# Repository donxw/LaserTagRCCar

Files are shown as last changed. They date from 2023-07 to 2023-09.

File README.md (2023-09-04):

# LaserTagRCCar
ESP Now based RC Car and controller with Laser and Photodetector to play Tag

CoverShot

Remote control car and joystick wireless controller with a display showing life left.  Each car has an LED (replaced the laser for child safety) and a photoresistor to sense a "hit".  The RC Car and controller communicate wirelessly using the ESP-NOW communication link.
## Bill of Materials
### Car
* 3D printed parts
* NodeMCU ESP8266 30pin Dev board
* ESP12E Motor Shield HW-588A.  Do not purchase an ESP8266 Motor Shield if it is not marked as HW-588A.
* 2x 6V, 500 RPM N20 Gearmotor.  Faster motors will work as well, but are more difficult to control (especially at low speeds)
* 9V USB rechargable LiPo battery
* 1x Neopixel LED (5mm, 3.3V)
* 1x Clear LED
* 1x Photoresistor (5506)
* 1x 20K Resistor
* 2x 73mm x 3mm O-ring (McMaster-Carr)
* Screws:
  * 1x M2x5
  * 5x M2x6
  * 2x M2x8
  * 3x M2.6x6
  * 2x M3x6
  * 2x M3x16
### Remote Control
* 3D printed parts
* TTGO T-Display ESP32 Board
* Joystick (https://www.mouser.com/ProductDetail/611-THB001P)
* 380 mAH Lipo battery
* Slide switch (https://www.aliexpress.us/item/2251832535125782.html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)

## Assembly
### Assemble Chassis
AssembleChassis_1
AssembleChassis_2
AssembleChassis_3

### Assemble Body
AssembleBody

### Car Wiring
Schematic
NeopixelLEDPinOut
CarWiring

### Remote Control Wiring
RemoteControlSchematic
16_WireRCParts

Slide Switch 
SlideSwitch-AliExpress

### Car Code
Before flasing the code to the car, the MAC of the ESP32 dev board in the Remote Control unit needs to be obtained and put into the ESP8266 arduino code for the car.  This can be done by uploading the code to the remote control unit ESP32 and watching the Serial Port for the MAC.  Copy this, and put the ESP32 address into the code for the ESP8266 of the car.  Now flash the car code and watch the Serial Port for the ESP8266 MAC.  Copy this and put it into the remote control unit ESP32 code, then re-flash the ESP32.

The car code is titled: "NodeMCUMotorShield_RCCar_Receiver_Laser_BiDir_Photosensor.ino".  Use board NodeMCU 1.0.

The remote control code is titled:  "Joystick_send_TTGO_BiDirectional.ino"  Use board ESP32 Dev Module.  This code uses the TFT_eSPI library for the TFT so update the User_Setup_Select.h file to uncomment this setup line only: #include <User_Setups/Setup25_TTGO_T_Display.h>.

Test to be sure the remote control and car communicate to each other before final assembly.

### Complete Car Assembly
After flashing the code to the car, place the body onto the chassis taking care to tuck wiring in without getting under the on-off push button.  Flip the car over to insert fasteners and the 9V usb rechargable battery.
AttachBodyandBattery

To assemble the front wheels, locate the smaller set of wheels and 2x M2 x 16 screws.  Take the screw and push them through the wheel holes to clean out the thin layer of support material left from printing.  Pushing the screw in from the reverse direction works fine.  Or use a 3mm drill bit and clean out the hole with a hand drill.  Once cleaned put a small drop of oil on the screw and push it in the correct direction - see image 3.
PrepIdleWheels

Attach the front wheels, taking care to be sure the wheels are aligned correctly.  Attache the rear wheels to the motor by aligning the flat side of the motor shaft to the flat part of the hole in the wheel.  Stretch the 75mm x 3mm o-ring over the wheels into the v-groove.  Snap on the hood scoop.
Wheels_Oring_Scoop

#### Assemble Remote Control
AssembleRemote

### Final car and remote control appearance 
Complete

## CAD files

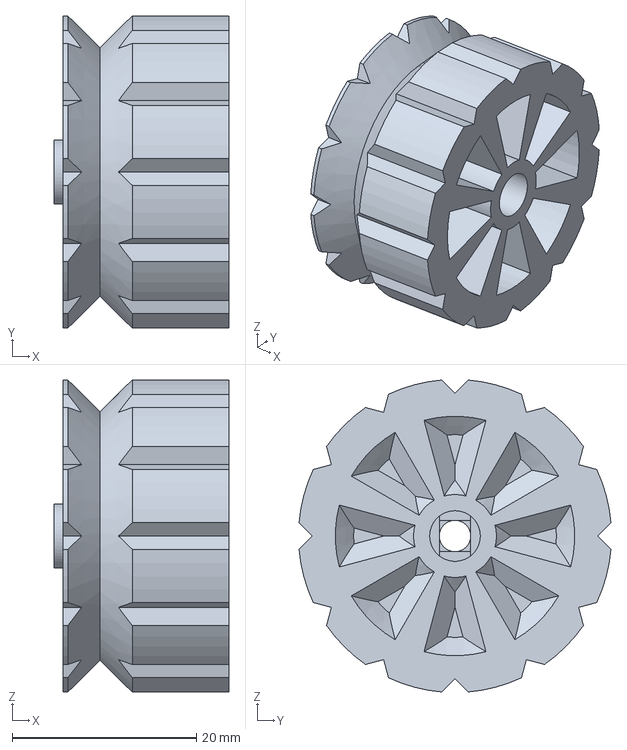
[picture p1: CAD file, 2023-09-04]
StepFiles/IdleWheel.step
19.0 x 33.9 x 33.9 mm

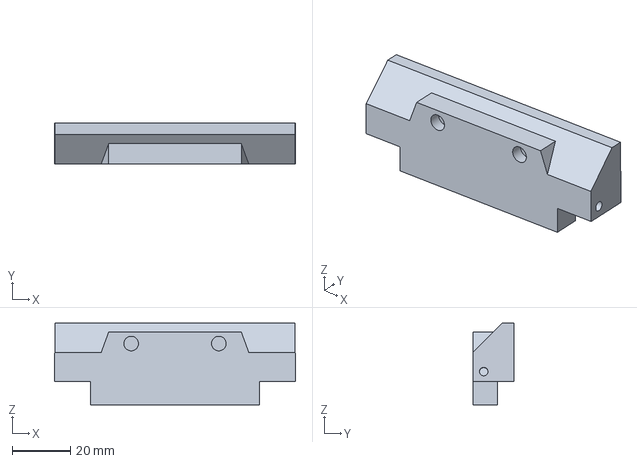
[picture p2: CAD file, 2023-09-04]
StepFiles/FrontAxle.step
82.5 x 14.0 x 28.0 mm

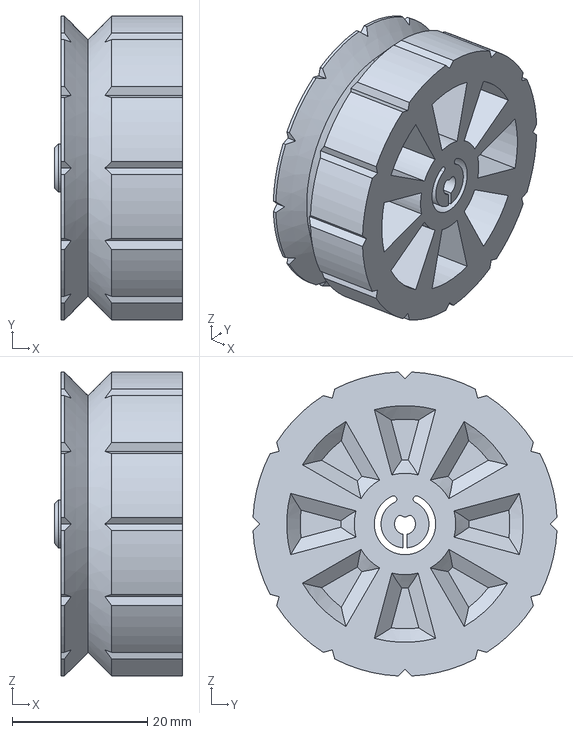
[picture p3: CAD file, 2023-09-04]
StepFiles/DriveWheel.step
19.0 x 45.0 x 45.0 mm

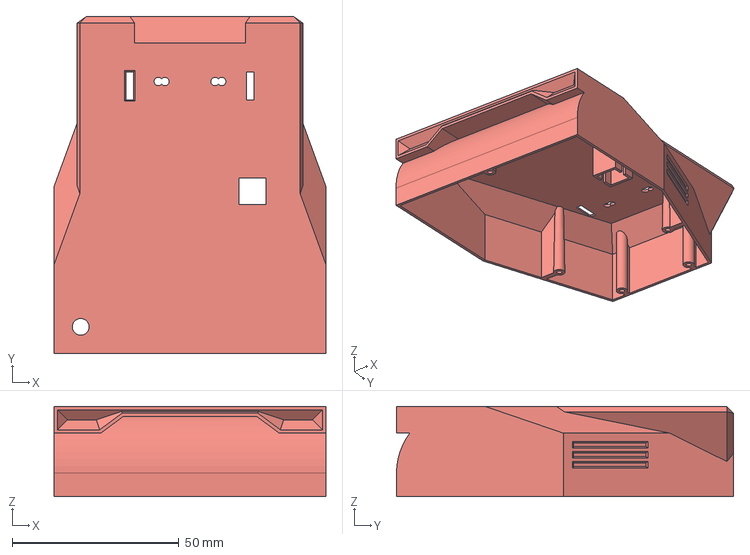
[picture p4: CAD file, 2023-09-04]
StepFiles/Body.step
81.5 x 101.0 x 27.0 mm

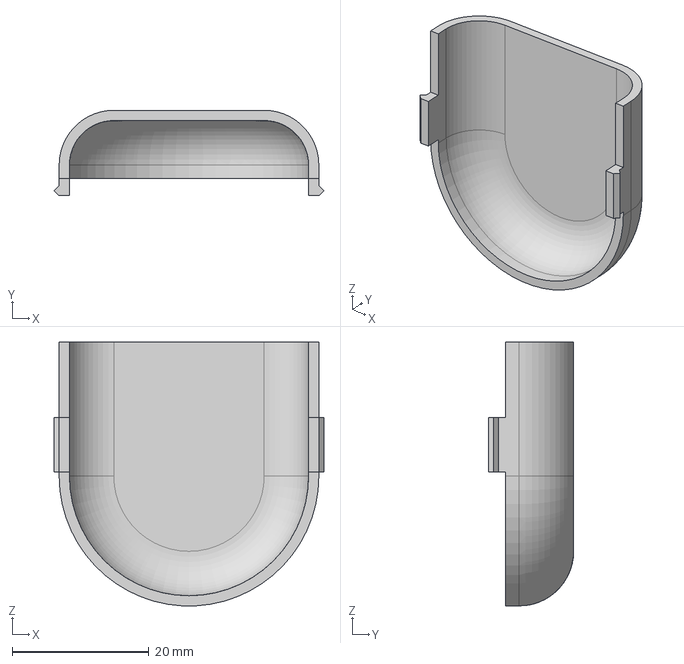
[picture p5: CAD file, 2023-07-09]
StepFiles/Scoop.step
39.5 x 12.5 x 38.6 mm

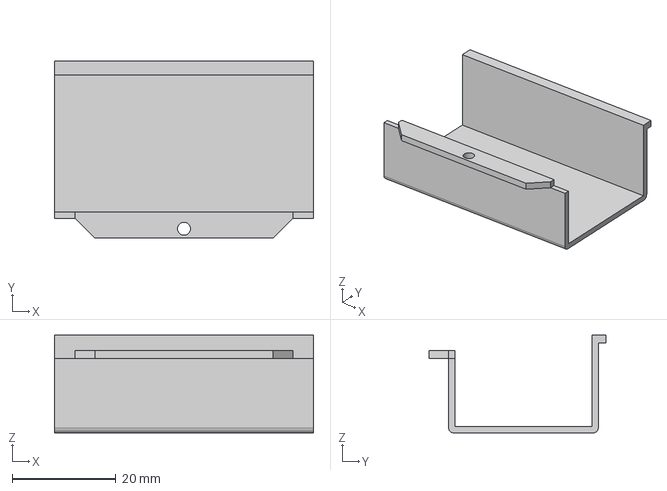
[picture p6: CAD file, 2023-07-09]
StepFiles/BatteryClip.step
50.0 x 34.2 x 18.9 mm

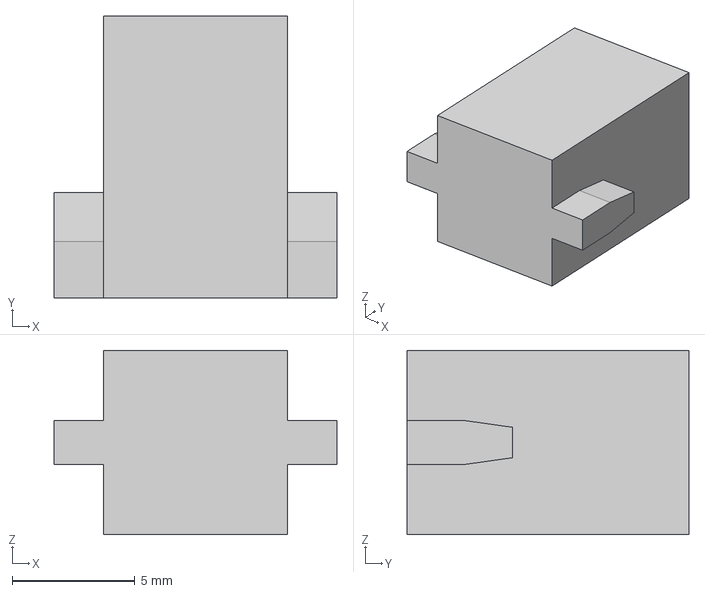
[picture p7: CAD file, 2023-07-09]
StepFiles/PushButton.step
11.5 x 11.5 x 7.50 mm

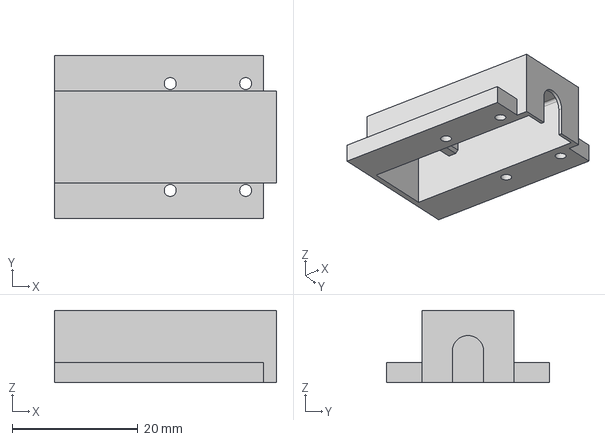
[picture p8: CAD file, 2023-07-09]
StepFiles/GearMotor Mount.step
35.3 x 25.9 x 11.5 mm

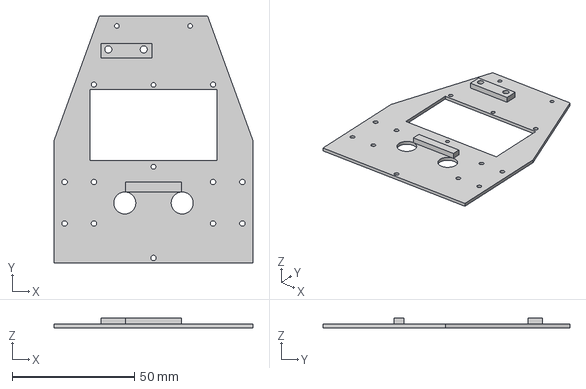
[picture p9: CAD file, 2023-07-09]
StepFiles/Chassis.step
81.5 x 101.0 x 4.00 mm

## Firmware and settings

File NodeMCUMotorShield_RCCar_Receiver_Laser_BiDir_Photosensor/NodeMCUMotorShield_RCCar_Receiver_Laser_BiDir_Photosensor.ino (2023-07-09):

// Visual Micro is in vMicro>General>Tutorial Mode
//
/*
    Name:       NodeMCUMotorShieldTest.ino
    Created:	9/26/2021 9:04:11 PM
    Author:     PAVGAMING\willi

    Board:  NodeMCU 1.0 
    Shield:  NodeMCU Motor Shield HW588A

    Wire Motor A to left motor
    Wire Motor B to right motor

    Shield I/O pins are
    Row closest to CPU = Digital
    Middle Row = 3.3V
    Outside Row = GND
*/

#include <Arduino.h>
#include <ESP8266WiFi.h>
#include <espnow.h>
#include <Wire.h>
#include <FastLED.h>

// Define User Types below here or use a .h file
//
#define DIRA 0  //D3
#define PWMA 5  //D1
#define DIRB 2  //D4
#define PWMB 4  //D2
#define CW 1
#define CCW 0

#define maxSpeed 255  // Max motor speed
#define deadBand 100  // Safe range to ignore round midpoint of joystick readings...
#define FORWARD 1
#define BACKWARD 2
#define DEBUG
//#define LEDPIN BUILTIN_LED

#define NEOPIN 14  //D5
#define N_LEDS 1
// Define the array of leds
CRGB leds[N_LEDS];

//  Global Variables
//
int LaserSensor = A0;
int SensorReading = 0;
int Laser = 12;  //D6
int HitCount = 0;

int dirMotorL = FORWARD;
int dirMotorR = FORWARD;
int motorSpeedL = 0;
int motorSpeedR = 0;
int speedDiff = 0;
const int valX_center = 1930;  // from testing the joystick center value
const int valY_center = 1900;
int full_range = 4095;  // full Joystick range from ESP32

//Set up MAC to send data to
// Concept B Contoller 08:3A:F2:69:CD:04 <- get from the Remote Control ESP32 Dev board
uint8_t mac_peer1[] = { 0x08, 0x3A, 0xF2, 0x69, 0xCD, 0x04 };

// Must match with the reciever on the remote control unit
struct SEND_DATA_STRUCTURE {
  int score;
};

SEND_DATA_STRUCTURE send;

void onDataSent(uint8_t* mac_addr, uint8_t sendStatus) {
  //Serial.print("\r\nLast Packet Send Status:\t");
  //Serial.println(sendStatus == 0 ? "Delivery Success" : "Delivery Fail");
}

// Set up data receiver

struct RECEIVE_DATA_STRUCTURE {
  int valX;
  int valY;
  int button;
};

RECEIVE_DATA_STRUCTURE received;
bool newMessage = false;

void onDataRecv(uint8_t* mac, uint8_t* incomingData, uint8_t len) {
  //Serial.println("Message received.");
  newMessage = true;
  // Transform the incoming data into our message structure
  memcpy(&received, incomingData, sizeof(received));
}

// Define Functions below here or use other .ino or cpp files
//
void playmelody();
void playmelody2();

// The setup() function runs once each time the micro-controller starts
void setup() {
  Serial.begin(115200);

  // Initialize Neopixel led
  //FastLED.addLeds<NEOPIXEL, NEOPIN>(leds, N_LEDS);  // GRB ordering is assumed
  FastLED.addLeds<WS2812, NEOPIN, RGB>(leds, N_LEDS);
  //FastLED.addLeds<WS2812, NEOPIN, BGR>(leds, N_LEDS);
  //FastLED.addLeds<WS2812, NEOPIN, GRB>(leds, N_LEDS);  // GRB ordering is typical
  //FastLED.addLeds<WS2812, NEOPIN, GBR>(leds, N_LEDS);  // GRB ordering is typical
  FastLED.setBrightness(32);
  leds[0] = CRGB::Black;
  FastLED.show();
  leds[0] = CRGB::DarkGreen;
  FastLED.show();

  // Laser ams Reciever
  pinMode(Laser, OUTPUT);
  pinMode(LaserSensor, INPUT);

  // Setup ESPNOW
  WiFi.disconnect();
  ESP.eraseConfig();

  // Wifi STA Mode
  WiFi.mode(WIFI_STA);

  // Get Mac Add  uncomment for debug
  Serial.print("\n");
  Serial.print("Mac Address: ");
  Serial.print(WiFi.macAddress());
  Serial.println("\nRC ESP-Now Receiver");

  // Initializing the ESP-NOW
  if (esp_now_init() != 0) {
    Serial.println("Problem during ESP-NOW init");
    return;
  }

  // Intialize ESPNow message
  received.valX = valX_center;
  received.valY = valY_center;
  received.button = true;

  // Set ESPNow Role
  //esp_now_set_self_role(ESP_NOW_ROLE_SLAVE);
  //
  // Register the receiver and sender callback functions
  esp_now_set_self_role(ESP_NOW_ROLE_CONTROLLER);
  esp_now_register_recv_cb(onDataRecv);
  esp_now_register_send_cb(onDataSent);

  // Register peer
  esp_now_add_peer(mac_peer1, ESP_NOW_ROLE_SLAVE, 1, NULL, 0);

  // Setup Motor Shield Pins
  pinMode(DIRA, OUTPUT);
  pinMode(PWMA, OUTPUT);
  pinMode(DIRB, OUTPUT);
  pinMode(PWMB, OUTPUT);

  playmelody();

  send.score = 0;
  esp_now_send(mac_peer1, (uint8_t*)&send, sizeof(send));

  // turn on built in LED
  //  pinMode(LEDPIN, OUTPUT);
  //  digitalWrite(LEDPIN, LOW);

  // plotter logo
  Serial.print(" ValY ValX Button ");

  // laser on
  digitalWrite(Laser, HIGH);
}

// Add the main program code into the continuous loop() function
void loop() {

  SensorReading = analogRead(LaserSensor);
  //Serial.println("Analog value : ");
  //Serial.println(SensorReading);
  if (SensorReading > 1020) {
    playmelody();
    Serial.println("Hit");
    HitCount++;
    send.score = HitCount;
    esp_now_send(mac_peer1, (uint8_t*)&send, sizeof(send));
    //    if (HitCount <= 3) {
    //      leds[0] = CRGB::DarkSeaGreen;
    //      FastLED.show();
    //    }
    if (HitCount == 4) {
      leds[0] = CRGB::LawnGreen;
      FastLED.show();
    }
    if (HitCount == 7) {
      leds[0] = CRGB::Orange;
      FastLED.show();
    }
    if (HitCount == 10) {
      leds[0] = CRGB::Red;
      FastLED.show();
      //spin motor
      digitalWrite(DIRA, CCW);  //Left Motor CCW for Forward
      analogWrite(PWMA, 220);
      digitalWrite(DIRB, CCW);  //Right Motor CCW for Backward
      analogWrite(PWMB, 220);
      playmelody2();
      //motor off
      analogWrite(PWMA, 0);
      analogWrite(PWMB, 0);
      // laser off
      digitalWrite(Laser, LOW);
    }
  } else {
    // nothing
  }

  // uncomment define DEBUG to run
#ifdef DEBUG
  if (newMessage == true) {
    Serial.print(received.valY);
    Serial.print(" ");
    Serial.print(received.valX);
    Serial.print(" ");
    Serial.print(received.button * 1000);
    Serial.print("\n");
    newMessage = false;
  }
#endif  // DEBUG
  // map joystick Y-axis to motor speed (deadband may not be needed since accounted for in sender)
  motorSpeedL = motorSpeedR = 0;
  if (received.valY < (valY_center - deadBand)) {
    motorSpeedL = map(received.valY, 0, valY_center, -maxSpeed, 0);
    motorSpeedR = motorSpeedL;
    Serial.println(motorSpeedL);
  } else if (received.valY > (valY_center + deadBand)) {
    motorSpeedL = map(received.valY, valY_center, full_range, 0, maxSpeed);
    motorSpeedR = motorSpeedL;
  }

  // determine speed difference in motors from joystick X-axis value
  speedDiff = 0;
  if (received.valX < valX_center - deadBand) {
    speedDiff = map(received.valX, 0, valX_center, -maxSpeed / 1, 0);
  } else if (received.valX > valX_center + deadBand) {
    speedDiff = map(received.valX, valX_center, full_range, 0, maxSpeed / 1);
  }

  // set Motor Speeds
  motorSpeedL += speedDiff;
  motorSpeedR -= speedDiff;

  dirMotorL = motorSpeedL < 0 ? BACKWARD : FORWARD;  //LEFT MOTOR_CH_A CCW IS FORWARD
  dirMotorR = motorSpeedR < 0 ? BACKWARD : FORWARD;  //RIGHT MOTOR_CH_B CW IS FORWARD

  // limit Motor Speeds to max value allowed
  motorSpeedL = abs(motorSpeedL);
  motorSpeedR = abs(motorSpeedR);
  if (motorSpeedL > maxSpeed) motorSpeedL = maxSpeed;
  if (motorSpeedR > maxSpeed) motorSpeedR = maxSpeed;

  // set Left motor speed & direction
  //dirMotorL == FORWARD ? M1.setmotor(_CCW, motorSpeedL) : M1.setmotor(_CW, motorSpeedL);
  if (dirMotorL == FORWARD) {
    digitalWrite(DIRA, CCW);  //Left Motor CCW for Forward
    analogWrite(PWMA, motorSpeedL);
  } else {
    digitalWrite(DIRA, CW);  //Left Motor CW for Reverse
    analogWrite(PWMA, motorSpeedL);
  }

  // set Right motor speed & direction
  //dirMotorR == FORWARD ? M2.setmotor(_CW, motorSpeedR) : M2.setmotor(_CCW, motorSpeedR);
  if (dirMotorR == FORWARD) {
    digitalWrite(DIRB, CW);  //Left Motor CW for Forward
    analogWrite(PWMB, motorSpeedR);
  } else {
    digitalWrite(DIRB, CCW);  //Left Motor CCW for Reverse
    analogWrite(PWMB, motorSpeedR);
  }

  // beep on button push
  if (received.button == false) {
    playmelody();
    Serial.println("beep beep");
    received.button = true;
  }



  delay(100);  //update @ 10Hz
}


/**
   # Colors
  CRGB::AliceBlue KEYWORD2
  CRGB::Amethyst  KEYWORD2
  CRGB::AntiqueWhite  KEYWORD2
  CRGB::Aqua  KEYWORD2
  CRGB::Aquamarine  KEYWORD2
  CRGB::Azure KEYWORD2
  CRGB::Beige KEYWORD2
  CRGB::Bisque  KEYWORD2
  CRGB::Black KEYWORD2
  CRGB::BlanchedAlmond  KEYWORD2
  CRGB::Blue  KEYWORD2
  CRGB::BlueViolet  KEYWORD2
  CRGB::Brown KEYWORD2
  CRGB::BurlyWood KEYWORD2
  CRGB::CadetBlue KEYWORD2
  CRGB::Chartreuse  KEYWORD2
  CRGB::Chocolate KEYWORD2
  CRGB::Coral KEYWORD2
  CRGB::CornflowerBlue  KEYWORD2
  CRGB::Cornsilk  KEYWORD2
  CRGB::Crimson KEYWORD2
  CRGB::Cyan  KEYWORD2
  CRGB::DarkBlue  KEYWORD2
  CRGB::DarkCyan  KEYWORD2
  CRGB::DarkGoldenrod KEYWORD2
  CRGB::DarkGray  KEYWORD2
  CRGB::DarkGreen KEYWORD2
  CRGB::DarkKhaki KEYWORD2
  CRGB::DarkMagenta KEYWORD2
  CRGB::DarkOliveGreen  KEYWORD2
  CRGB::DarkOrange  KEYWORD2
  CRGB::DarkOrchid  KEYWORD2
  CRGB::DarkRed KEYWORD2
  CRGB::DarkSalmon  KEYWORD2
  CRGB::DarkSeaGreen  KEYWORD2
  CRGB::DarkSlateBlue KEYWORD2
  CRGB::DarkSlateGray KEYWORD2
  CRGB::DarkTurquoise KEYWORD2
  CRGB::DarkViolet  KEYWORD2
  CRGB::DeepPink  KEYWORD2
  CRGB::DeepSkyBlue KEYWORD2
  CRGB::DimGray KEYWORD2
  CRGB::DodgerBlue  KEYWORD2
  CRGB::FireBrick KEYWORD2
  CRGB::FloralWhite KEYWORD2
  CRGB::ForestGreen KEYWORD2
  CRGB::Fuchsia KEYWORD2
  CRGB::Gainsboro KEYWORD2
  CRGB::GhostWhite  KEYWORD2
  CRGB::Gold  KEYWORD2
  CRGB::Goldenrod KEYWORD2
  CRGB::Gray  KEYWORD2
  CRGB::Green KEYWORD2
  CRGB::GreenYellow KEYWORD2
  CRGB::Honeydew  KEYWORD2
  CRGB::HotPink KEYWORD2
  CRGB::IndianRed KEYWORD2
  CRGB::Indigo  KEYWORD2
  CRGB::Ivory KEYWORD2
  CRGB::Khaki KEYWORD2
  CRGB::Lavender  KEYWORD2
  CRGB::LavenderBlush KEYWORD2
  CRGB::LawnGreen KEYWORD2
  CRGB::LemonChiffon  KEYWORD2
  CRGB::LightBlue KEYWORD2
  CRGB::LightCoral  KEYWORD2
  CRGB::LightCyan KEYWORD2
  CRGB::LightGoldenrodYellow  KEYWORD2
  CRGB::LightGreen  KEYWORD2
  CRGB::LightGrey KEYWORD2
  CRGB::LightPink KEYWORD2
  CRGB::LightSalmon KEYWORD2
  CRGB::LightSeaGreen KEYWORD2
  CRGB::LightSkyBlue  KEYWORD2
  CRGB::LightSlateGray  KEYWORD2
  CRGB::LightSteelBlue  KEYWORD2
  CRGB::LightYellow KEYWORD2
  CRGB::Lime  KEYWORD2
  CRGB::LimeGreen KEYWORD2
  CRGB::Linen KEYWORD2
  CRGB::Magenta KEYWORD2
  CRGB::Maroon  KEYWORD2
  CRGB::MediumAquamarine  KEYWORD2
  CRGB::MediumBlue  KEYWORD2
  CRGB::MediumOrchid  KEYWORD2
  CRGB::MediumPurple  KEYWORD2
  CRGB::MediumSeaGreen  KEYWORD2
  CRGB::MediumSlateBlue KEYWORD2
  CRGB::MediumSpringGreen KEYWORD2
  CRGB::MediumTurquoise KEYWORD2
  CRGB::MediumVioletRed KEYWORD2
  CRGB::MidnightBlue  KEYWORD2
  CRGB::MintCream KEYWORD2
  CRGB::MistyRose KEYWORD2
  CRGB::Moccasin  KEYWORD2
  CRGB::NavajoWhite KEYWORD2
  CRGB::Navy  KEYWORD2
  CRGB::OldLace KEYWORD2
  CRGB::Olive KEYWORD2
  CRGB::OliveDrab KEYWORD2
  CRGB::Orange  KEYWORD2
  CRGB::OrangeRed KEYWORD2
  CRGB::Orchid  KEYWORD2
  CRGB::PaleGoldenrod KEYWORD2
  CRGB::PaleGreen KEYWORD2
  CRGB::PaleTurquoise KEYWORD2
  CRGB::PaleVioletRed KEYWORD2
  CRGB::PapayaWhip  KEYWORD2
  CRGB::PeachPuff KEYWORD2
  CRGB::Peru  KEYWORD2
  CRGB::Pink  KEYWORD2
  CRGB::Plaid KEYWORD2
  CRGB::Plum  KEYWORD2
  CRGB::PowderBlue  KEYWORD2
  CRGB::Purple  KEYWORD2
  CRGB::Red KEYWORD2
  CRGB::RosyBrown KEYWORD2
  CRGB::RoyalBlue KEYWORD2
  CRGB::SaddleBrown KEYWORD2
  CRGB::Salmon  KEYWORD2
  CRGB::SandyBrown  KEYWORD2
  CRGB::SeaGreen  KEYWORD2
  CRGB::Seashell  KEYWORD2
  CRGB::Sienna  KEYWORD2
  CRGB::Silver  KEYWORD2
  CRGB::SkyBlue KEYWORD2
  CRGB::SlateBlue KEYWORD2
  CRGB::SlateGray KEYWORD2
  CRGB::Snow  KEYWORD2
  CRGB::SpringGreen KEYWORD2
  CRGB::SteelBlue KEYWORD2
  CRGB::Tan KEYWORD2
  CRGB::Teal  KEYWORD2
  CRGB::Thistle KEYWORD2
  CRGB::Tomato  KEYWORD2
  CRGB::Turquoise KEYWORD2
  CRGB::Violet  KEYWORD2
  CRGB::Wheat KEYWORD2
  CRGB::White KEYWORD2
  CRGB::WhiteSmoke  KEYWORD2
  CRGB::Yellow  KEYWORD2
  CRGB::YellowGreen KEYWORD2
  **/

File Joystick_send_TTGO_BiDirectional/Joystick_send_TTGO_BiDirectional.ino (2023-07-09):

/* Joystick

This program simply captures joystick every 10ms and sends to RCCar via espnow

for ttgo t display esp32
int const JOYSTICK_BTN = 17;
int const JOYSTICK_AXIS_X = 33;
int const JOYSTICK_AXIS_Y = 36;

On ESP32:
These pins do not support analog input when WiFi is in use: 00, 02, 04, 12, 13, 14, 15, 25, 26,
These ones do: 32, 33, 34, 35, 36, 39, Use one of these last 6 to connect your sensor.

For the TTGO T-Display, use board ESP32 Dev Module

*/

// TFT Display Libraries
#include <SPI.h>
#include <TFT_eSPI.h>

TFT_eSPI tft = TFT_eSPI();  // tft instance
uint16_t fg = TFT_WHITE;
uint16_t bg = TFT_BLACK;
#define GFXFF 1
#define CF_NB07 &NotoSans_Bold7pt7b
#define CF_NB08 &NotoSans_Bold8pt7b
#define CF_NB15 &NotoSans_Bold15pt7b
#define CF_NB36 &NotoSans_Bold36pt7b


// ESP Now Libraries
#include <WiFi.h>
#include <esp_now.h>

// Sender MAC
// Car B 84:CC:A8:9A:EB:BB <- get from target car ESP8266 devboard
uint8_t mac_peer1[] = { 0x84, 0xCC, 0xA8, 0x9A, 0xEB, 0xBB };

esp_now_peer_info_t peer1;

struct SEND_DATA_STRUCTURE {
  //put your variable definitions here for the data you want to send
  //THIS MUST BE EXACTLY THE SAME ON THE OTHER ARDUINO
  int valX;
  int valY;
  int button;
};

//give a name to the group of data
SEND_DATA_STRUCTURE myMessage;

// callback when data is sent
void OnDataSent(const uint8_t *mac_addr, esp_now_send_status_t status) {
  //Serial.print("\r\nLast Packet Send Status:\t");
  //Serial.println(status == ESP_NOW_SEND_SUCCESS ? "Delivery Success" : "Delivery Fail");
}

// Set up Receiver - MUST MATCH SEND_DATA_STRUCTURE FROM 8266 STATION

struct RECEIVE_DATA_STRUCTURE {
  int score;
};

RECEIVE_DATA_STRUCTURE received;
bool newMessage = false;

void OnDataRecv(const uint8_t *mac, const uint8_t *incomingData, int len) {
  memcpy(&received, incomingData, sizeof(received));
  newMessage = true;
  //Serial.println("newMessage received");
}

//ttgo t display - if WiFi.h is used, then only ADC0 (GPIO36), ADC3 (39), ADC4 (32), ADC5 (33) can be used.
int const JOYSTICK_BTN = 17;
int const JOYSTICK_AXIS_X = 33;
int const JOYSTICK_AXIS_Y = 36;

//===============================================================================
//  Initialization
//===============================================================================

void setup() {

  //Set all button pins as inputs with internal pullup resistors enabled.
  pinMode(JOYSTICK_BTN, INPUT_PULLUP);

  Serial.begin(9600);

  tft.begin();
  tft.setRotation(0);
  tft.setTextColor(TFT_WHITE, TFT_DARKGREEN);
  tft.fillScreen(TFT_DARKGREEN);
  tft.setFreeFont(CF_NB36);
  // set middle center font datum
  tft.setTextDatum(MC_DATUM);
  tft.setTextPadding(80);
  tft.drawString("?", 65, 120);

  WiFi.mode(WIFI_STA);

  // Get Mac Add
  Serial.print("\n");
  Serial.print("Mac Address: ");
  Serial.print(WiFi.macAddress());
  Serial.println("\nRC ESP-Now Receiver");

  // Initializing the ESP-NOW
  if (esp_now_init() != 0) {
    Serial.println("Problem during ESP-NOW init");
    return;
  }

  memcpy(peer1.peer_addr, mac_peer1, 6);
  peer1.channel = 0;
  // Register the peer
  Serial.println("Registering a peer 1");
  if (esp_now_add_peer(&peer1) == ESP_OK) {
    Serial.println("Peer 1 added");
  }

  esp_now_register_send_cb(OnDataSent);
  esp_now_register_recv_cb(OnDataRecv);
}
//===============================================================================
//  Main
//===============================================================================
void loop() {
  // Check each button input and print the status to the Serial Monitor Window
  //Serial.print("\tJOYSTICK BTN="), Serial.print(digitalRead(JOYSTICK_BTN));
  myMessage.button = digitalRead(JOYSTICK_BTN);

  // Print the full X/Y joystick values (0-1023)
  //myMessage.valX = map(analogRead(JOYSTICK_AXIS_X), 0, 4096, 0, 1024);
  myMessage.valX = analogRead(JOYSTICK_AXIS_X);
  //Serial.print("\tX="), Serial.print(myMessage.valX);  //esp32 range - map to use with arduino uno reciever

  //myMessage.valY = map(analogRead(JOYSTICK_AXIS_Y), 0, 4096, 0, 1024);
  myMessage.valY = analogRead(JOYSTICK_AXIS_Y);
  //Serial.print("\tY="), Serial.println(myMessage.valY);

  esp_now_send(NULL, (uint8_t *)&myMessage, sizeof(myMessage));

  // Check if a new message has been received

  if (newMessage == true) {
    newMessage = false;
    Serial.printf("Score: %d \n", received.score);
    int life = 10 - received.score;
    Serial.printf("life: %d \n", life);
    if (life >= 7) {
      tft.setTextColor(TFT_WHITE, TFT_DARKGREEN);
      tft.fillScreen(TFT_DARKGREEN);
      tft.setFreeFont(CF_NB36);
      // set middle center datum
      tft.setTextDatum(MC_DATUM);
      tft.setTextPadding(80);
      tft.drawNumber(life, 65, 120);
    }
    if (life < 7 && life >= 4) {
      tft.setTextColor(TFT_WHITE, TFT_GREEN);
      tft.fillScreen(TFT_GREEN);
      tft.setFreeFont(CF_NB36);
      // set middle center datum
      tft.setTextDatum(MC_DATUM);
      tft.setTextPadding(80);
      tft.drawNumber(life, 65, 120);
    }
    if (life < 4 && life >= 1) {
      tft.setTextColor(TFT_WHITE, TFT_ORANGE);
      tft.fillScreen(TFT_ORANGE);
      tft.setFreeFont(CF_NB36);
      // set middle center datum
      tft.setTextDatum(MC_DATUM);
      tft.setTextPadding(80);
      tft.drawNumber(life, 65, 120);
    }
    if (life <= 0) {
      tft.setTextColor(TFT_WHITE, TFT_RED);
      tft.fillScreen(TFT_RED);
      tft.setFreeFont(CF_NB36);
      // set middle center datum
      tft.setTextDatum(MC_DATUM);
      tft.setTextPadding(80);
      tft.drawNumber(life, 65, 120);
    }
  }

  delay(50);
}
